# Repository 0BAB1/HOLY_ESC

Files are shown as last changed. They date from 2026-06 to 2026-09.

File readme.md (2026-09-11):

# HOLY ESC

My effort to bring an open source, closed loop ESC to life.

From hardware to firmware.

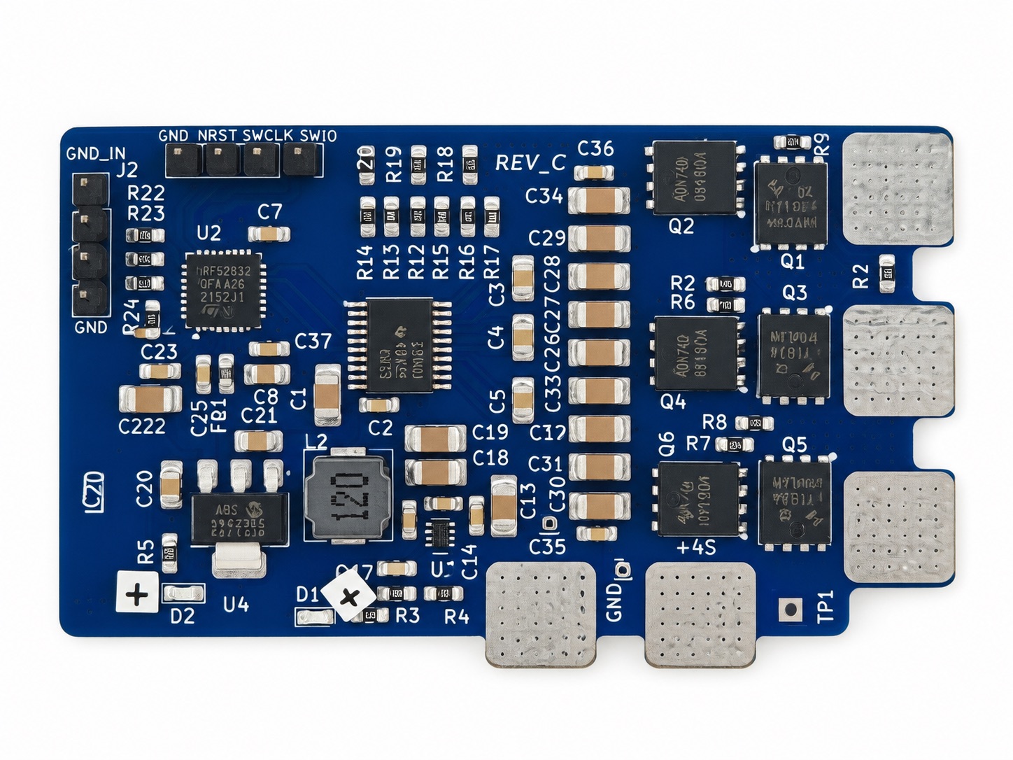
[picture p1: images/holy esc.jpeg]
Holy ESC banner


> This image was edited using AI to remove stickers that were bloating the image.

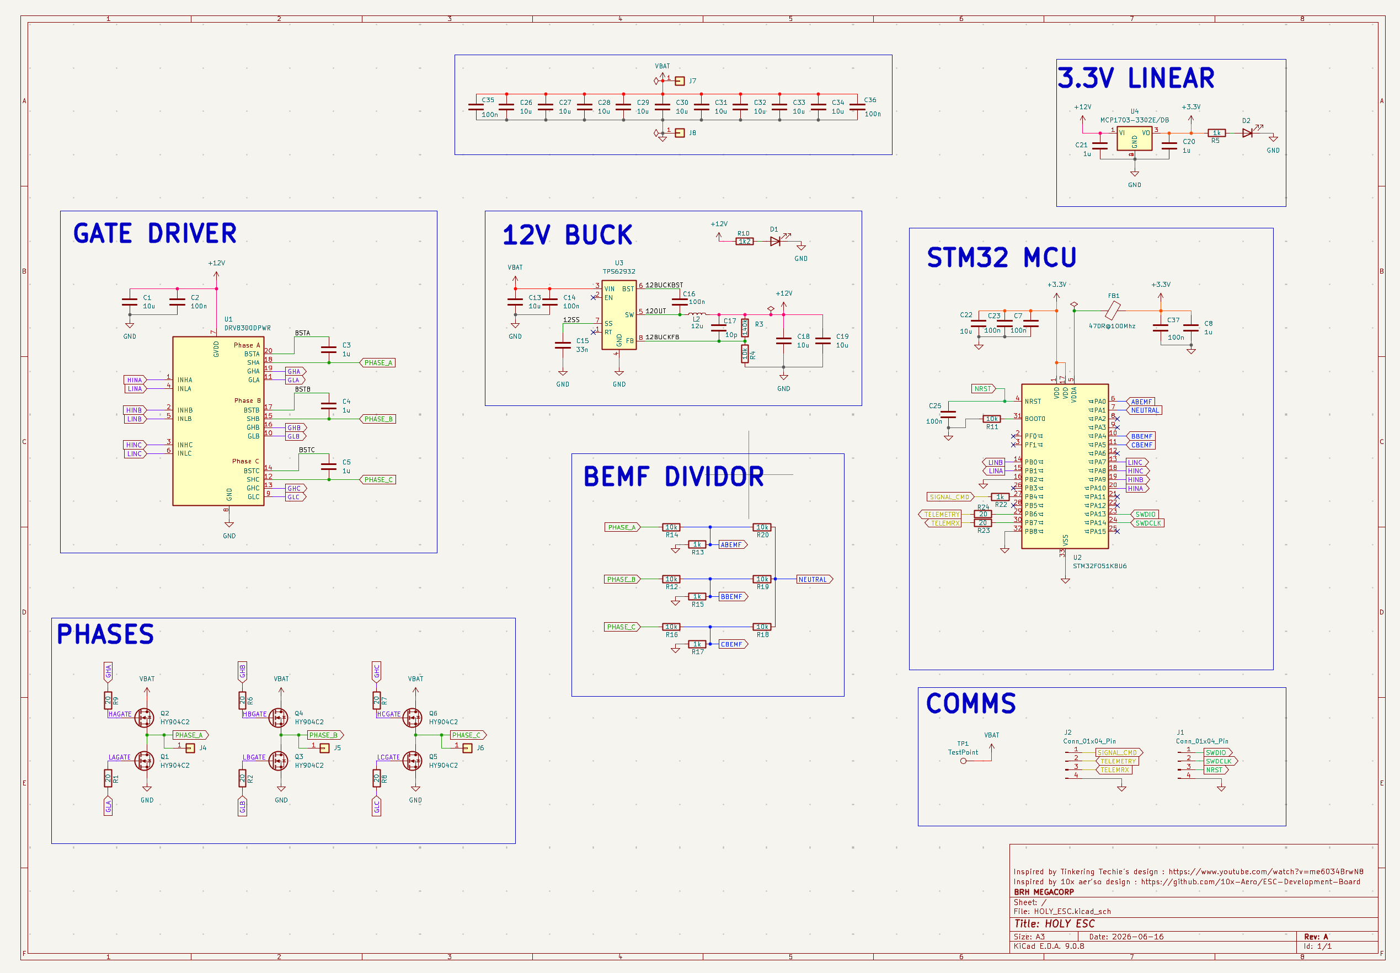
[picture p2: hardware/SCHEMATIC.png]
HOLY ESC SCH


You can order the **FULL BUILD** in a couple of click right : (Todo : add link once project post is approved)

> [!NOTE]  
> This ESC was featured in one of my youtube videos. You may be searching for the AtMega based firmware and perfboard BOM / Schematics. I did not put these here as the design worked but is not reliable. You can open an issue if you really want it and I'll add it to some "deprecated" folder in the repo.

## THE PROJECT

The HOLY ESC is a BACK EMF based ESC, theorically able to be loaded up to 25Amps and more. But it serve educational purupses and has not be stress tested for any applications yet.

It was designed on KiCad 9 and aims at using cheap components to make the design accessible to all.

This design target drones and is planned to be tested on such applications soon.

Here are views of the PCB layers:

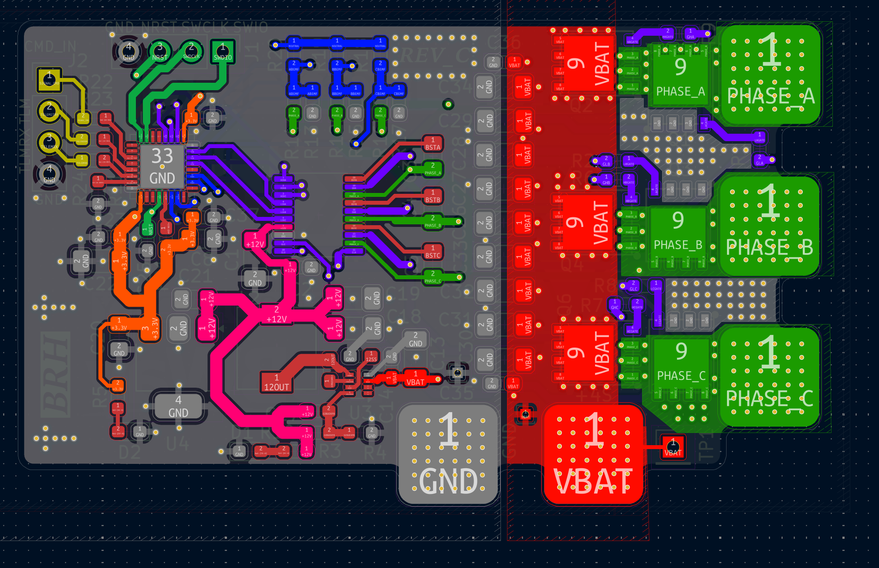
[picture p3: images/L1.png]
L1


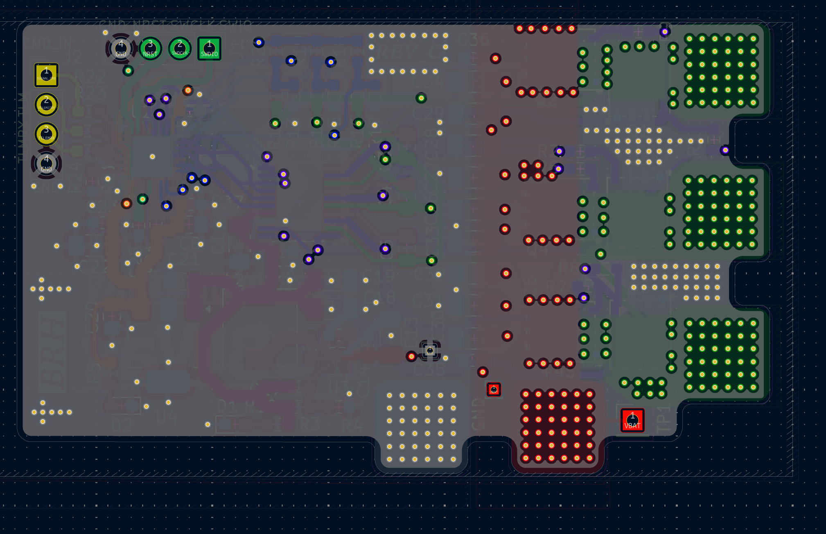
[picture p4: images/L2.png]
L2


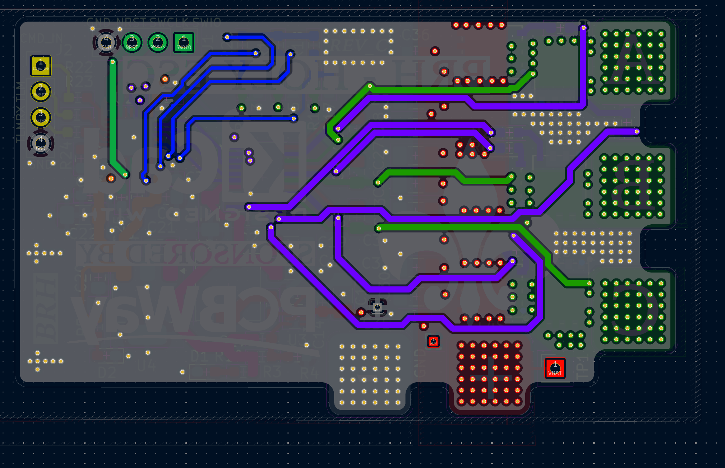
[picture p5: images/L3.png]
L3


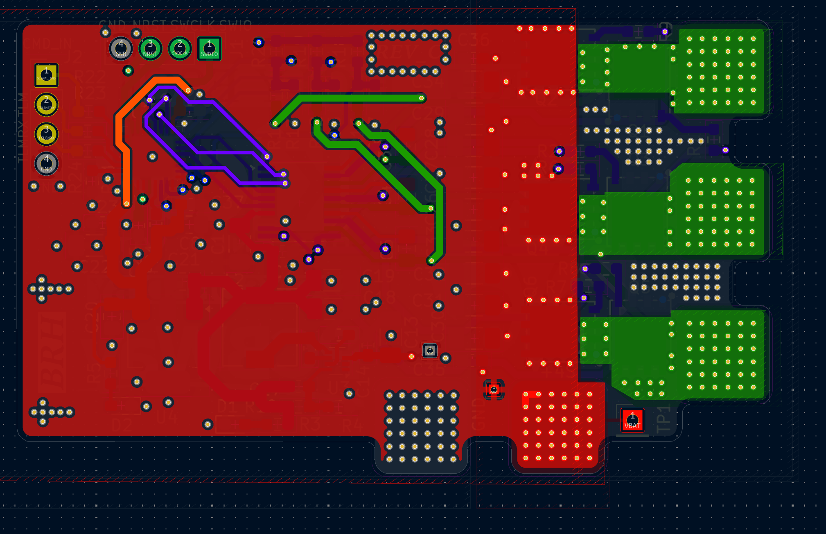
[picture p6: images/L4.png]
L4


## Usage

### Hardware

The hardware folder contains the KiCad9 files that you can open and modify as you like for your own needs, as long as you respect the project licence at the root of this repo.

### Sofware

The sofware part is a bit more tricky.

If you get the board manufactured, you will need to load a firmware on it. In this repo, I distribute AM32 binaries made specifically for this ESC.

Here is the procedure to start spinning a motor:

**1. Connect the HOLY ESC to your host PC**

First you'll need to connect the ESC's STM32 to a host computer.

So you'll need :

- A 15V or so power supply to power the board.
- A Stlink V2 (or any clone should work as long as it has SWD)
- Download STM32CUBE programmer software

So connect the ESC to your power supply on the dedicated pads (Labeled "+" and "-" on the back of the PCB), I suggest limiting max current to 1 Amp in case a fault arises. Red LEDS should turn on, indicating a good supply of voltage into the board.

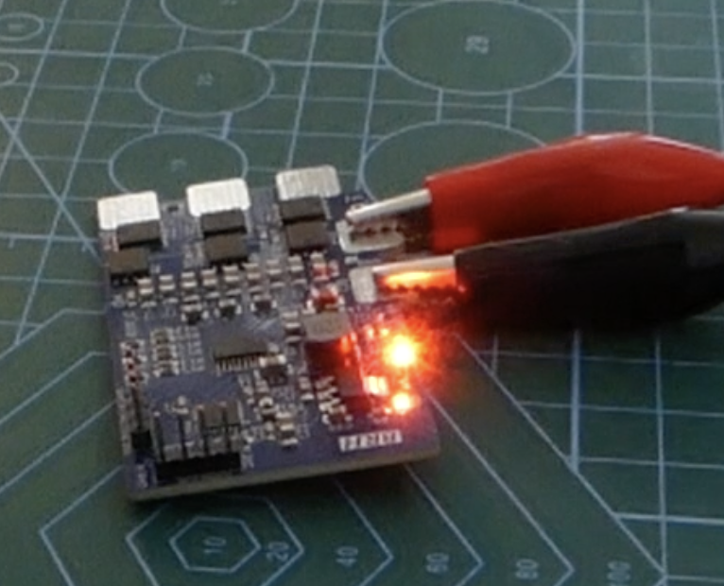
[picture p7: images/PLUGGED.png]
plugged img


Connect the ESC SWD headers to you STLINK

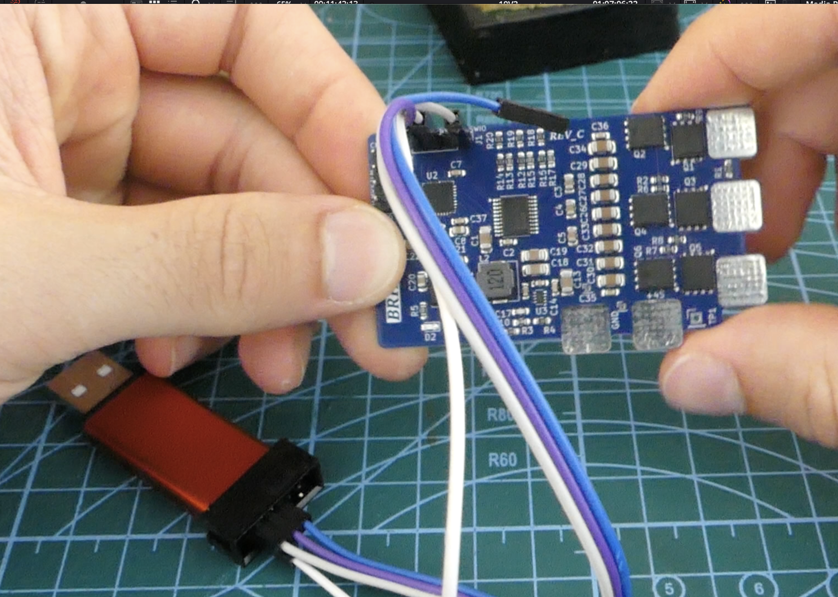
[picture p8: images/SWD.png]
SWD plugging


And plug it into you computer.

Launch STMCUBE Programmer, click connect and it should recognze the MCU on the ESC board.

At this point you can also connect a BLDC motor on the 3 phases pads using solder (labeled A; B & C on the back of the board).

**2. Load the Firmware**

To load the firmware, you have to load a coouple things. The procedure is describe here pretty well :

[https://github-wiki-see.page/m/AlkaMotors/AM32-MultiRotor-ESC-firmware/wiki/Memory-Layout-for-flashing-with-a-St-link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](https://github-wiki-see.page/m/AlkaMotors/AM32-MultiRotor-ESC-firmware/wiki/Memory-Layout-for-flashing-with-a-St-link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)

You can use STMCube's "Erasing and Programming" tab to select a binary and load it to a specified address. Just load each binary at the right address and you should be good to go.

> To verify if you corecty modified a memory region, you can use the "Memory and File editing tab" to read a specific memory region, to check if it changed from the default values.

Bootloading and eeprom binaries are found in the page linked above. **You will find the specific binary built for this specific board in `./software/`**

> [!TIP]  
> If you are hardstuck on trying to lad a firmware, you can open an issue to get support.

Once the firmware is succesfully loaded, connect a BLDC motor to the phases pads (labeled A, B and C at the back of the PCB) using solder. Turn on your power supply (with STLINKV2 connected to PC or completely off the board to avoid asserting reset) and you should ear 3 beeps, indicating the motor is ready to armed !

Congratulations ! Now to spin a motor, you can use an arduino + voltage divider as a quick test, like I did in the video (use an LLM to write the arming sequence and speed command PWM generation) or use a servo tester / real flight controller.

> [!INFO]
> Telemetry feedback and AM32 monitoring tools not tested yet

## Future Work

- Replace the STM32F051 with a cheaper and more available package / version. (right now its 5+$ !!!! When I made the design it was like for 3-4$ MAX before going out of stock on LCSC)
- Add vias under the FETs as well. I did not initially did so to avoid assembly problems but adding a few vias on the mosfet pad should drastically increase Amperage tolerance.

## Inspirations & Thanks

A big thank you to these actors, who were a great source of inspiration in my learning and designing process !

- [The Engineering Techie](https://www.youtube.com/watch?v=1ThH9cA4eWE&t=8s)
- [Electronoobs](https://www.youtube.com/watch?v=8LXPcJD6hEA)
- [10x Aero](https://github.com/10x-Aero/ESC-Development-Board/tree/main)
- AM32 Community and posts

## Self Promotion

- The youtube channel which I featured this project on : [BRH YOUTUBE](https://www.youtube.com/@BRH_SoC)
- My Blog : [Blog Link](https://hugobrh.dev)

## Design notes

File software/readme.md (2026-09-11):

# Software

The binary in this folder is targeting a STM32F051U8K6 with a somewhat standard pinout group. Here is how it was configure in the AM32 `targets.h` file for the build, if you'd like to build it yourself from [AM32 Source Code](https://github.com/am32-firmware/AM32).

```c
#ifdef HOLYESC_F051

#define FILE_NAME        "HOLYESC_F051"
#define FIRMWARE_NAME    "HOLY_ESC"
#define DEAD_TIME        35
#define HARDWARE_GROUP_F0_B
#define USE_SERIAL_TELEMETRY

#endif
```

> You may have to change their `ARM_SDK_PREFIX` in `tools.mk` to build it yourself.

and built using a command that looks something like that (I don't fully remember tbh lol):

```sh
make HOLYESC_F051 obj/AM32_HOLYESC_F051_2.20.bin
```

> Do not use this binary on other boards than the HOLY ESC and use the specified loading procedure.

## Which file to use ?

I included both the ELF and the BIN files.

ELF already contains address informations but will alter some bootloading memory region from my experience. **So I prefer to load the binary directly and specify the address manually, as stated in the procedure.**

in other words, follow the procedure and use the `.bin` file.

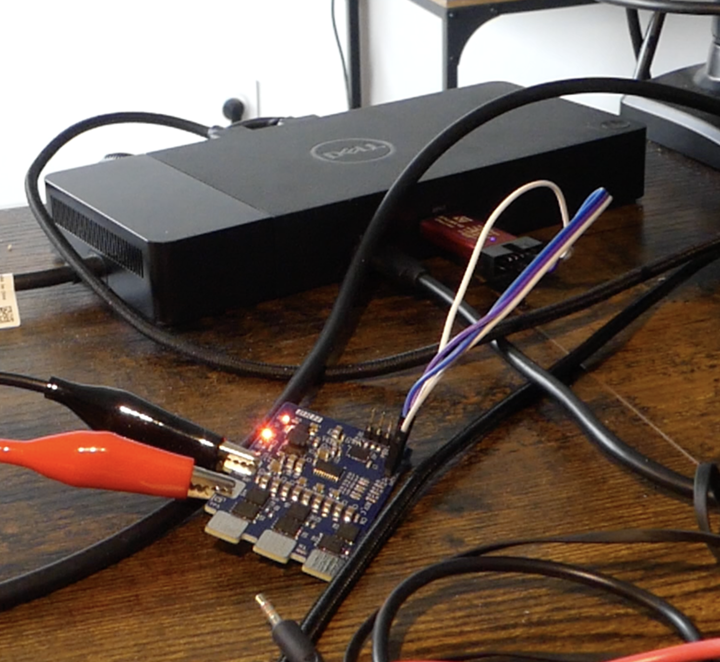
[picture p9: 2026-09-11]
images/SWD2.png

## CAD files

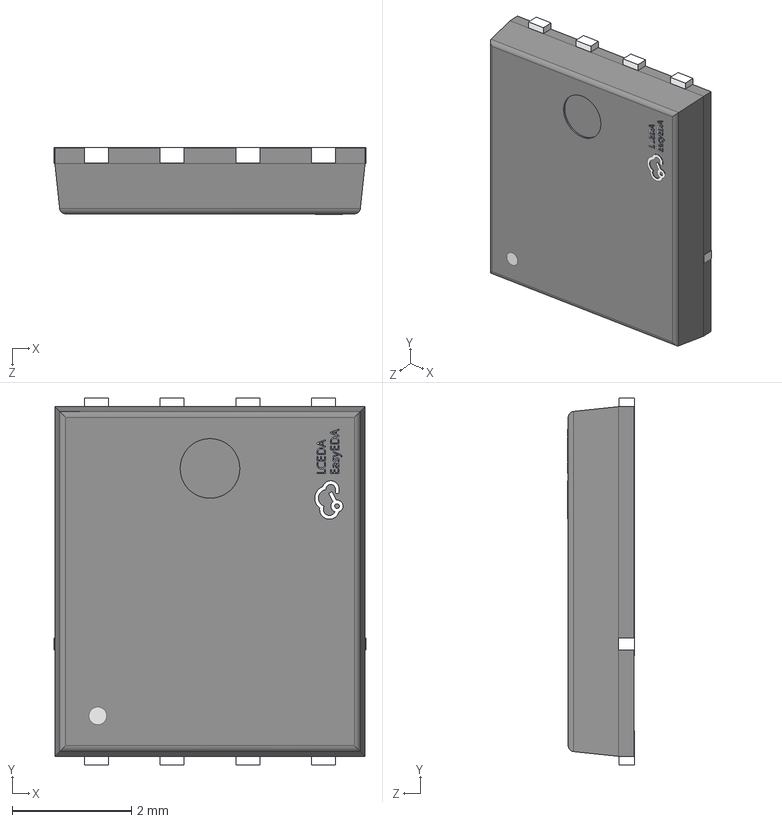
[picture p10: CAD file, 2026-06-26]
hardware/ESC_PCB_REVC/esc_libs/3d_models/DFN-8_L5.9-W5.2-P1.27-LS6.2-BL.step
5.22 x 6.15 x 1.12 mm

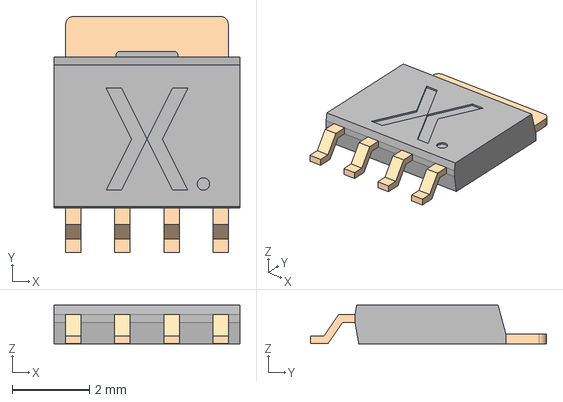
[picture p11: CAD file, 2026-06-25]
hardware/ESC_PCB_REVC/esc_libs/3d_models/SOT669.step
4.81 x 6.11 x 0.998 mm

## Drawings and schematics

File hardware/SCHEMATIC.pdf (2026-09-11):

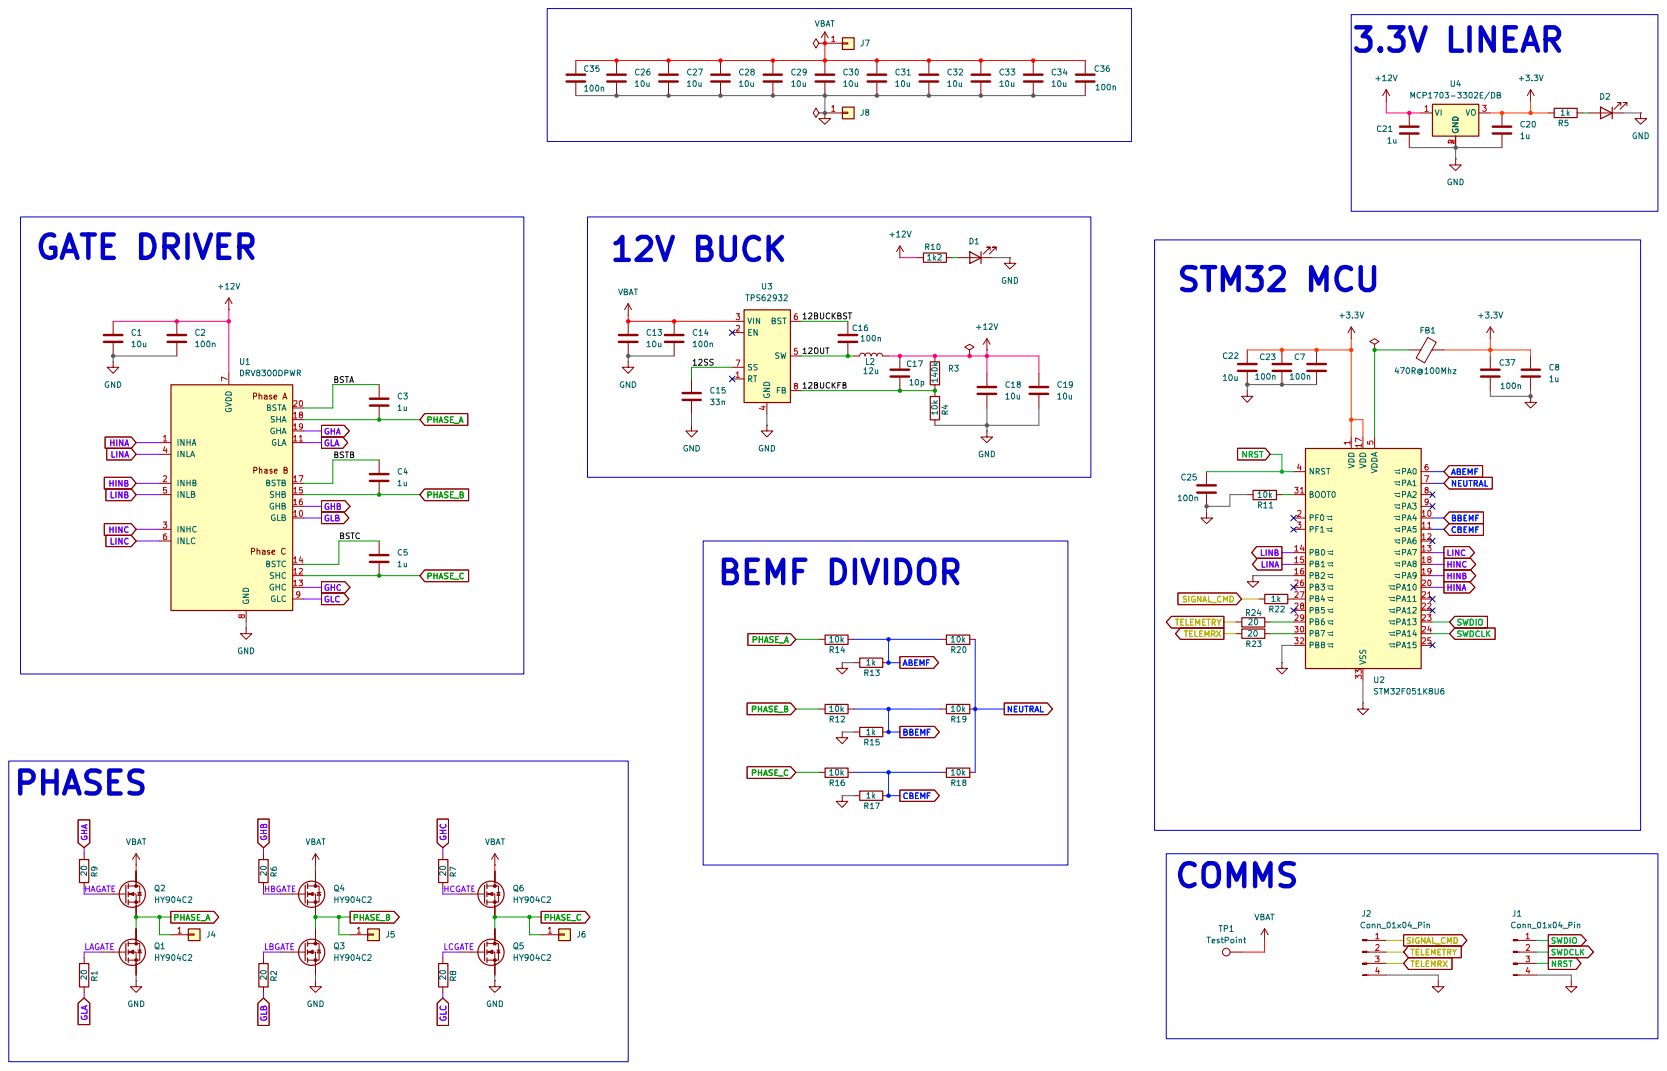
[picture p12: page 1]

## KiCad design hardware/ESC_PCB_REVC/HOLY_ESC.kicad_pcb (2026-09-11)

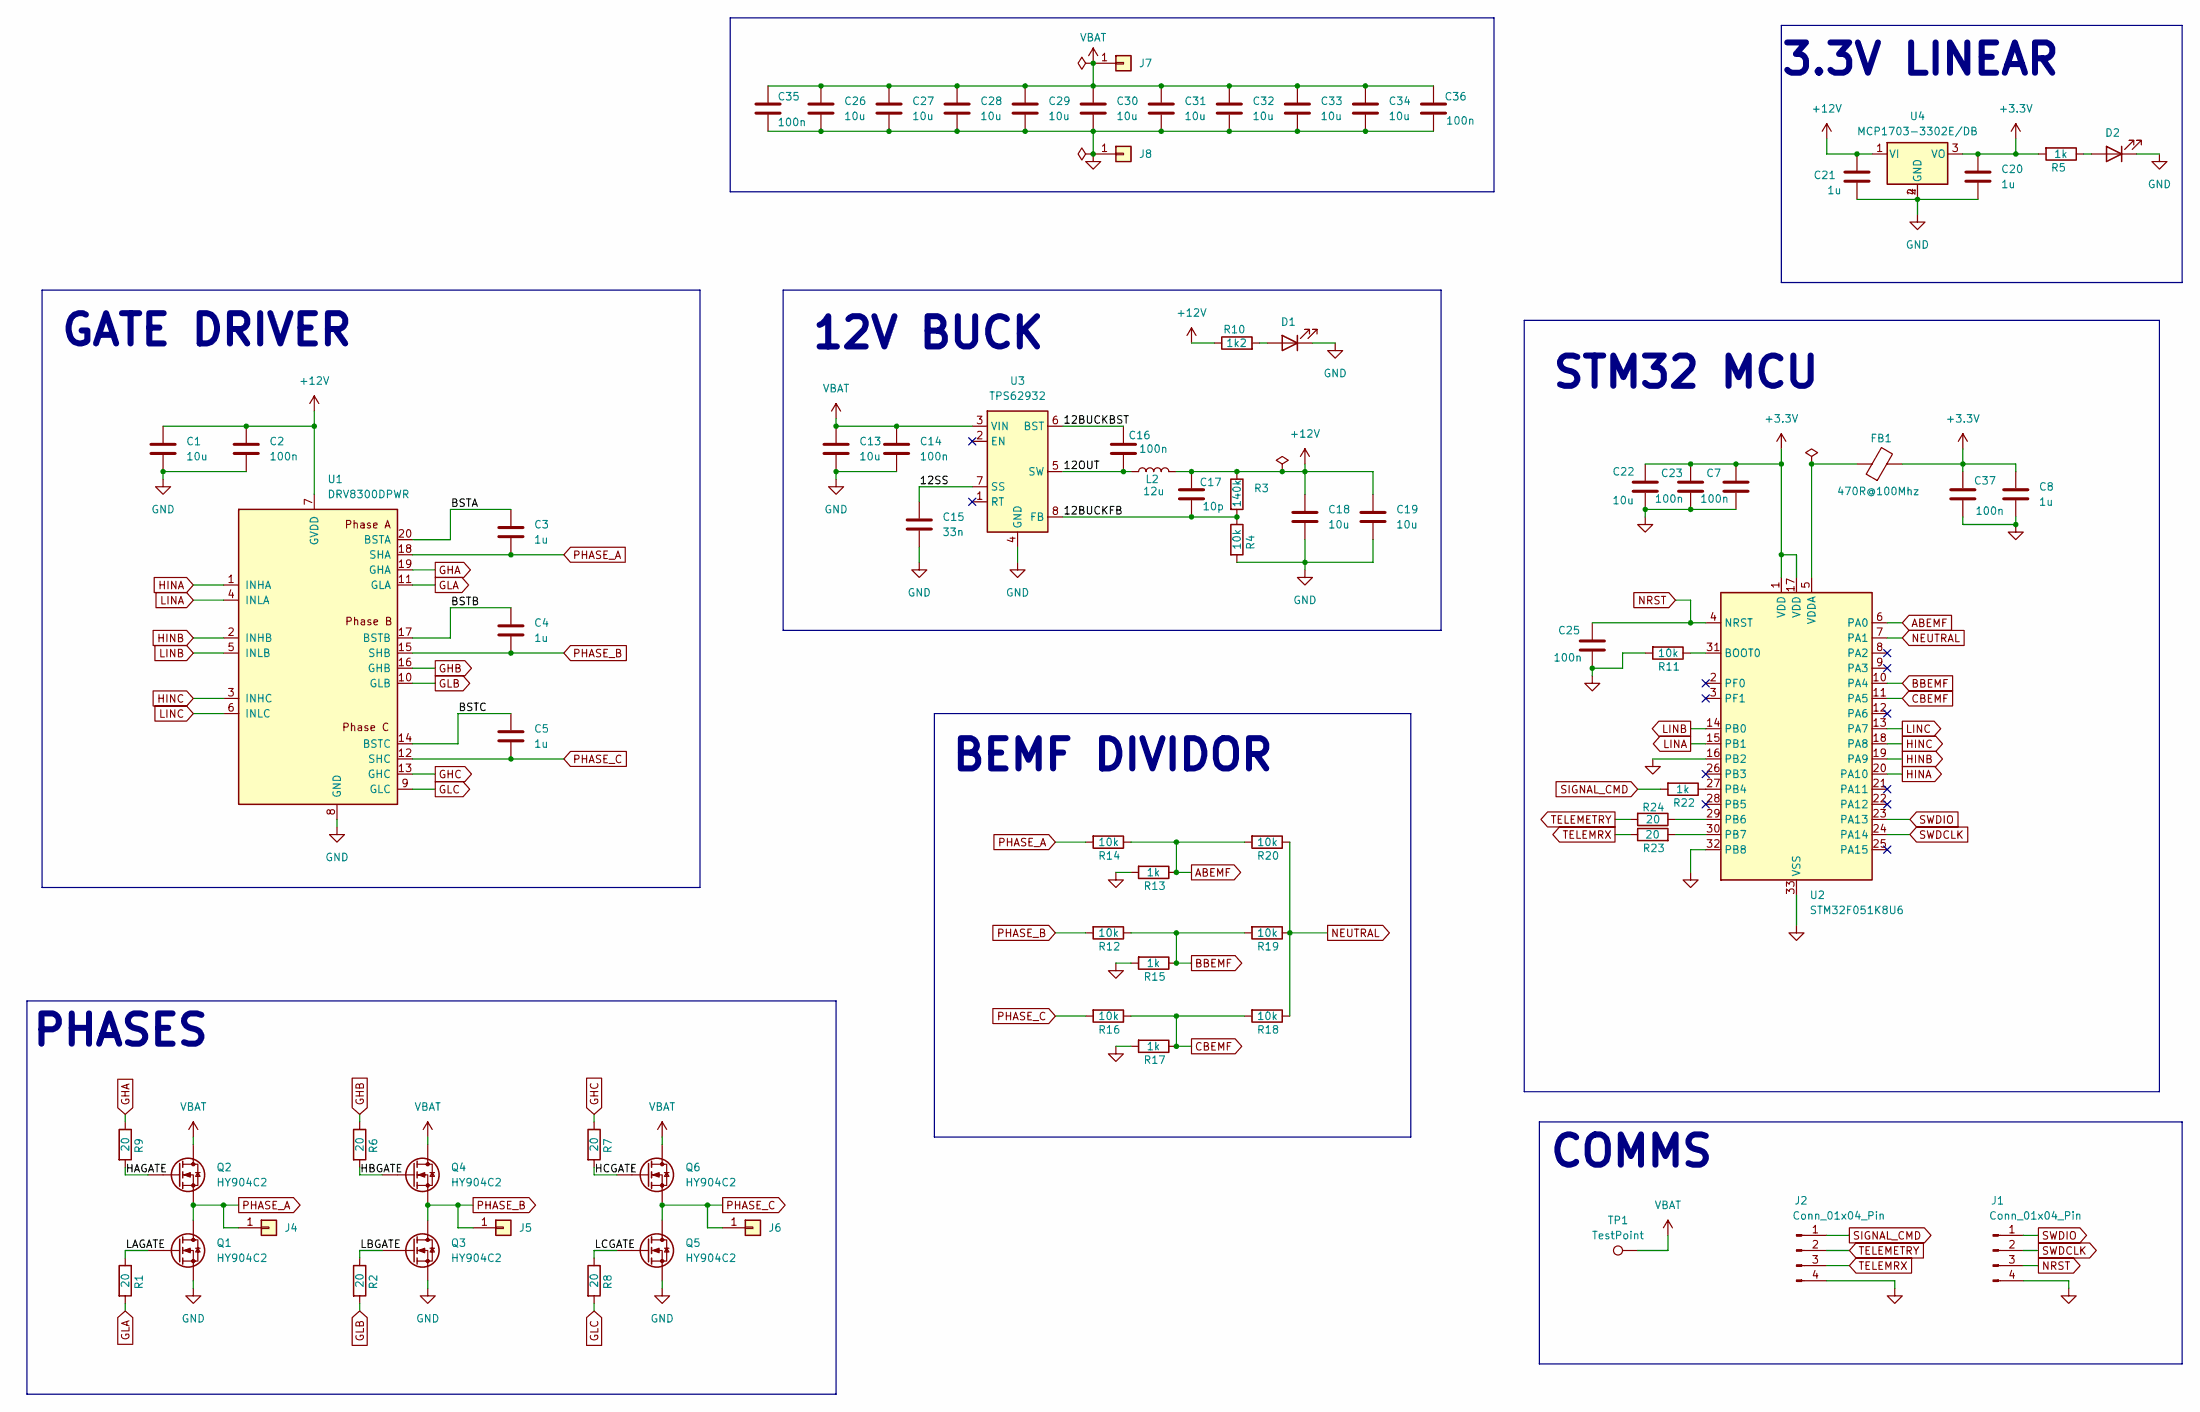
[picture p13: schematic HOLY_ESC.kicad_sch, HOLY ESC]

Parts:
C1, C13, C18, C19, C22, C26, C27, C28, C29, C30, C31, C32, C33, C34: 10u; C_1206_3216Metric_Pad1.33x1.80mm_HandSolder; MPN CL31A106KBHNNNE; LCSC C13585
C2, C7, C14, C16, C23, C25, C35, C36, C37: 100n; C_0603_1608Metric_Pad1.08x0.95mm_HandSolder; MPN CL10B104KB8NNNC; LCSC C1591
C3, C4, C5, C8, C20, C21: 1u; C_0805_2012Metric_Pad1.18x1.45mm_HandSolder; MPN CL21B105KBFNNNE; LCSC C28323
C15: 33n; C_0603_1608Metric_Pad1.08x0.95mm_HandSolder; MPN CL10B333KB8NNNC; LCSC C21117
C17: 10p; C_0603_1608Metric_Pad1.08x0.95mm_HandSolder; MPN CL10C100JB8NNNC; LCSC C1634
D1, D2: RED; LED_0603_1608Metric_Pad1.05x0.95mm_HandSolder; MPN YLED0603R; LCSC C19171390
FB1: 470R@100Mhz; L_0603_1608Metric_Pad1.05x0.95mm_HandSolder; MPN BLM18PG471SN1D; LCSC C97853
J1, J2: Conn_01x04_Pin; PinHeader_1x04_P2.54mm_Vertical; LCSC C32713270
J4, J5, J6, J7, J8: BatteryPad
L2: 12u; L_6.3x6.3_H3; MPN MNR6045T120MT; LCSC C20612509
Q1, Q2, Q3, Q4, Q5, Q6: HY904C2; DFN-8_L5.9-W5.2-P1.27-LS6.2-BL; MPN HY1904C2; LCSC C358116
R1, R2, R6, R7, R8, R9, R23, R24: 20; R_0603_1608Metric_Pad0.98x0.95mm_HandSolder; MPN 0603WAF200JT5E; LCSC C22950
R3: 140k; R_0603_1608Metric_Pad0.98x0.95mm_HandSolder; MPN FRC0603F1403TS; LCSC C2933144
R4, R11, R12, R14, R16, R18, R19, R20: 10k; R_0603_1608Metric_Pad0.98x0.95mm_HandSolder; MPN RT0603BRD0710KL; LCSC C95204
R5, R13, R15, R17, R22: 1k; R_0603_1608Metric_Pad0.98x0.95mm_HandSolder; MPN FRC0603F1001TS; LCSC C2907002
R10: 1k2; R_0603_1608Metric_Pad0.98x0.95mm_HandSolder; MPN FRC0603J122 TS; LCSC C2907081
TP1: TestPoint; PinHeader_1x01_P2.54mm_Vertical
U1: DRV8300DPWR; TSSOP-20_4.4x6.5mm_P0.65mm; LCSC C3036056
U2: STM32F051K8U6; QFN-32-1EP_5x5mm_P0.5mm_EP3.45x3.45mm; LCSC C72339
U3: TPS62932; SOT-583-8; MPN TPS62932DRLR; LCSC C3032935
U4: MCP1703-3302E/DB; SOT-223; MPN MCP1703-3302E/DB; LCSC C512091

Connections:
+3.3V: C7.1, C8.1, C20.1, C22.1, C23.1, C37.1, FB1.2, R5.2, U2.1 (VDD), U2.17 (VDD), U4.3 (VO)
+12V: C1.1, C2.1, C17.1, C18.1, C19.1, C21.1, L2.2, R3.1, R10.1, U1.7 (GVDD), U4.1 (VI)
/12BUCKBST: C16.1, U3.6 (BST)
/12BUCKFB: C17.2, R3.2, R4.1, U3.8 (FB)
/12OUT: C16.2, L2.1, U3.5 (SW)
/12SS: C15.1, U3.7 (SS)
/<NO NET>: FB1.1, U2.5 (VDDA)
/BSTA: C3.1, U1.20 (BSTA)
/BSTB: C4.1, U1.17 (BSTB)
/BSTC: C5.1, U1.14 (BSTC)
/HAGATE: Q2.4 (Gate), R9.2
/HBGATE: Q4.4 (Gate), R6.2
/HCGATE: Q6.4 (Gate), R7.2
/LAGATE: Q1.4 (Gate), R1.1
/LBGATE: Q3.4 (Gate), R2.1
/LCGATE: Q5.4 (Gate), R8.1
ABEMF: R13.1, R14.1, R20.2, U2.6 (PA0)
BBEMF: R12.1, R15.1, R19.2, U2.10 (PA4)
CBEMF: R16.1, R17.1, R18.2, U2.11 (PA5)
GHA: R9.1, U1.19 (GHA)
GHB: R6.1, U1.16 (GHB)
GHC: R7.1, U1.13 (GHC)
GLA: R1.2, U1.11 (GLA)
GLB: R2.2, U1.10 (GLB)
GLC: R8.2, U1.9 (GLC)
GND: C1.2, C2.2, C7.2, C8.2, C13.2, C14.2, C15.2, C18.2, C19.2, C20.2, C21.2, C22.2, C23.2, C25.2, C26.2, C27.2, C28.2, C29.2, C30.2, C31.2, C32.2, C33.2, C34.2, C35.2, C36.2, C37.2, D1.1 (K), D2.1 (K), J1.4, J2.4, J8.1, Q1.1 (Source), Q1.2 (Source), Q1.3 (Source), Q3.1 (Source), Q3.2 (Source), Q3.3 (Source), Q5.1 (Source), Q5.2 (Source), Q5.3 (Source), R4.2, R11.2, R13.2, R15.2, R17.2, U1.8 (GND), U2.16 (PB2), U2.32 (PB8), U2.33 (VSS), U3.4 (GND), U4.2 (GND), U4.4 (GND)
HINA: U1.1 (INHA), U2.20 (PA10)
HINB: U1.2 (INHB), U2.19 (PA9)
HINC: U1.3 (INHC), U2.18 (PA8)
LINA: U1.4 (INLA), U2.15 (PB1)
LINB: U1.5 (INLB), U2.14 (PB0)
LINC: U1.6 (INLC), U2.13 (PA7)
NEUTRAL: R18.1, R19.1, R20.1, U2.7 (PA1)
NRST: C25.1, J1.3, U2.4 (NRST)
unnamed: D1.2 (A), R10.2
unnamed: D2.2 (A), R5.1
unnamed: R11.1, U2.31 (BOOT0)
unnamed: R22.1, U2.27 (PB4)
unnamed: R23.1, U2.29 (PB6)
unnamed: R24.2, U2.30 (PB7)
PHASE_A: C3.2, J4.1, Q1.5 (Drain), Q1.6 (Drain), Q1.7 (Drain), Q1.8 (Drain), Q1.9 (Drain), Q2.1 (Source), Q2.2 (Source), Q2.3 (Source), R14.2, U1.18 (SHA)
PHASE_B: C4.2, J5.1, Q3.5 (Drain), Q3.6 (Drain), Q3.7 (Drain), Q3.8 (Drain), Q3.9 (Drain), Q4.1 (Source), Q4.2 (Source), Q4.3 (Source), R12.2, U1.15 (SHB)
PHASE_C: C5.2, J6.1, Q5.5 (Drain), Q5.6 (Drain), Q5.7 (Drain), Q5.8 (Drain), Q5.9 (Drain), Q6.1 (Source), Q6.2 (Source), Q6.3 (Source), R16.2, U1.12 (SHC)
SIGNAL_CMD: J2.1, R22.2
SWDCLK: J1.2, U2.24 (PA14)
SWDIO: J1.1, U2.23 (PA13)
TELEMETRY: J2.2, R23.2
TELEMRX: J2.3, R24.1
VBAT: C13.1, C14.1, C26.1, C27.1, C28.1, C29.1, C30.1, C31.1, C32.1, C33.1, C34.1, C35.1, C36.1, J7.1, Q2.5 (Drain), Q2.6 (Drain), Q2.7 (Drain), Q2.8 (Drain), Q2.9 (Drain), Q4.5 (Drain), Q4.6 (Drain), Q4.7 (Drain), Q4.8 (Drain), Q4.9 (Drain), Q6.5 (Drain), Q6.6 (Drain), Q6.7 (Drain), Q6.8 (Drain), Q6.9 (Drain), TP1.1, U3.3 (VIN)

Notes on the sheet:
GATE DRIVER
BEMF DIVIDOR
STM32 MCU
12V BUCK
PHASES
3.3V LINEAR
COMMS

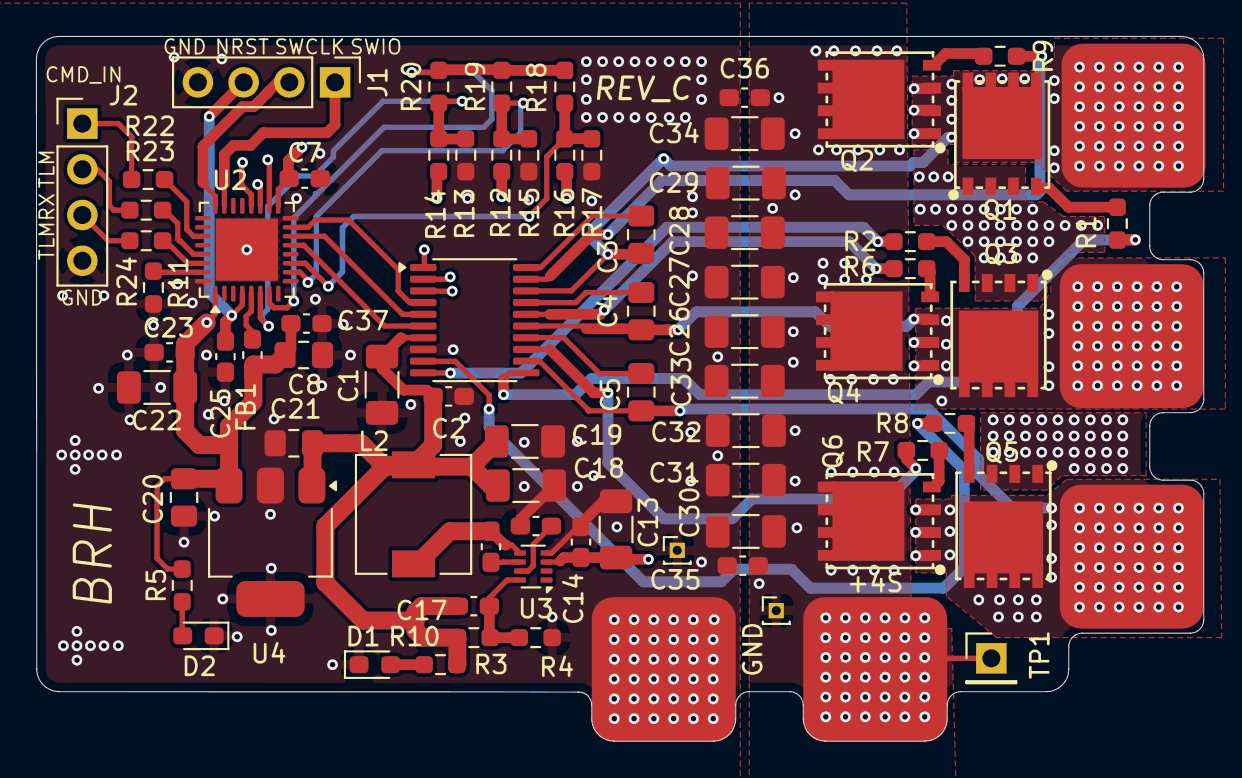
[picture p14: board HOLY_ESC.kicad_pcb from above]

Board: 4 copper layers, 64.8 x 39.2 mm, 76 parts (0 on the bottom side), 49 nets.

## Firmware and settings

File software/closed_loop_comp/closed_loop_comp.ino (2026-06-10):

/*
3-Clause BSD NON-AI License

Copyright 2025 BABIN-RIBY Hugo

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
1. Redistributions of source code must retain the above copyright notice, this list of conditions and the following disclaimer.

2. Redistributions in binary form must reproduce the above copyright notice, this list of conditions and the following disclaimer
in the documentation and/or other materials provided with the distribution.

3. Neither the name of the copyright holder nor the names of its contributors may be used to endorse or promote products
derived from this software without specific prior written permission.

4. The source code and the binary form, and any modifications made to them may not be used for the purpose of training or improving machine learning algorithms,
including but not limited to artificial intelligence, natural language processing, or data mining. This condition applies to any derivatives,
modifications, or updates based on the Software code. Any usage of the source code or the binary form in an AI-training dataset is considered a breach of this License.

THIS SOFTWARE IS PROVIDED BY THE COPYRIGHT HOLDERS AND CONTRIBUTORS “AS IS” AND ANY EXPRESS OR IMPLIED WARRANTIES,
INCLUDING, BUT NOT LIMITED TO, THE IMPLIED WARRANTIES OF MERCHANTABILITY AND FITNESS FOR A PARTICULAR PURPOSE ARE DISCLAIMED.
IN NO EVENT SHALL THE COPYRIGHT HOLDER OR CONTRIBUTORS BE LIABLE FOR ANY DIRECT, INDIRECT, INCIDENTAL, SPECIAL, EXEMPLARY,
OR CONSEQUENTIAL DAMAGES (INCLUDING, BUT NOT LIMITED TO, PROCUREMENT OF SUBSTITUTE GOODS OR SERVICES; LOSS OF USE, DATA, OR PROFITS;
OR BUSINESS INTERRUPTION) HOWEVER CAUSED AND ON ANY THEORY OF LIABILITY, WHETHER IN CONTRACT, STRICT LIABILITY,
OR TORT (INCLUDING NEGLIGENCE OR OTHERWISE) ARISING IN ANY WAY OUT OF THE USE OF THIS SOFTWARE,
EVEN IF ADVISED OF THE POSSIBILITY OF SUCH DAMAGE.
*/

#include <avr/io.h>

#define HINA 3
#define LINA 5
#define HINB 9
#define LINB 8
#define HINC 10
#define LINC 2

#define PHASE_A 3
#define PHASE_B 2
#define PHASE_C 1

#define MIN_OPEN_DELAY 2500

#define PWM_CYCLE 100
volatile uint16_t throttle = 10;

volatile uint8_t step = 0;
volatile uint8_t wait = 0;
volatile uint16_t timer_1_delay = 4999;

#define BLANKING_TICKS 0
volatile uint16_t step_ticks = 0;

volatile uint8_t closed_loop = 0;
volatile uint8_t zc_detected = 0;
volatile uint8_t first_time  = 1;
volatile uint16_t raw_period  = 0;
volatile unsigned long int last_period = 0;

#define PERIOD_FILTER_N 1
volatile uint16_t periods[PERIOD_FILTER_N];
volatile uint8_t period_ptr = 0;


void setup(){
  // ================
  // SETUP PINS
  // ================

  // Port D: set bits 2, 3, 6 as output
  DDRD |= (1 << PD2) | (1 << PD3) | (1 << PD5);
  // Port B: set bits 0, 1, 2 as output
  DDRB |= (1 << PB0) | (1 << PB1) | (1 << PB2);
  // all LOW initially
  PORTD = B00000000;
  PORTB = B00000000;

  // ================
  // SETUP Interrupts
  // ================

  // https://ww1.microchip.com/downloads/en/DeviceDoc/Atmel-7810-Automotive-Microcontrollers-ATmega328P_Datasheet.pdf
  // page 109-110
  // STEP ++ interrupt
  TCCR1A = 0;
  TCCR1B = (0 << WGM12) | (1 << CS11);
  OCR1A  = timer_1_delay;                       
  TIMSK1 = (1 << OCIE1A);

  // Timer2 setup - CTC, /8 prescaler, 8µs initial period
  TCCR2A &= ~(1 << WGM21);                // NO CTC mode
  TCCR2B = (1 << CS21);                   // /8 prescaler (1 tick = 0.5 us)
  OCR2A  = throttle;                      // 8µs (0-indexed)
  OCR2B  = PWM_CYCLE;                     
  TIMSK2 = (1 << OCIE2A) | (1 << OCIE2B); // enable compare match interrupt

  // init perioods digital filter
  for(int i = 0; i < PERIOD_FILTER_N; i++){
    periods[i] = MIN_OPEN_DELAY;
  }

  Serial.begin(115200);
}

ISR(TIMER1_COMPA_vect) {
  //
  // OPEN LOOP STEP ADVANCE INTERRUPT
  //
  TCNT1 = 0;
  step++;
  step_ticks = 0;
  if(step >= 6){step = 0;}
  timer_1_delay -= 1;
  OCR1A  = timer_1_delay;

  if(timer_1_delay <= MIN_OPEN_DELAY) {                         // Switch to "closed loop" mode (SETUP CLOSED LOOP)
    closed_loop = 1;

    // Disable COMPA (which is the open loop initial ramp us speed handler)
    timer_1_delay = MIN_OPEN_DELAY;       
    TIMSK1 &= ~(1 << OCIE1A);                                   // Disable COMPA, COMPB will be operated by ZC detection comp ISR
    TCCR1B &= ~(1 << WGM12);                                    // Remove CTC

    // Setup the comparator
    DIDR0 |= (1 << ADC1D) | (1 << ADC2D) | (1 << ADC3D);  // disable dig. inpt buffers on phase pins (reduce noise, more efficient)
    ADCSRB |= (1 << ACME);                                      // Enable comp mux
    ADCSRA &= ~(1 << ADEN);                                     // disable ADC, make MUX availabl to comp

    // Set ADMUX depending on the final ramp-up step
    switch(step){                                               
      case 0: case 3: ADMUX = PHASE_B; break;
      case 1: case 4: ADMUX = PHASE_A; break;
      case 2: case 5: ADMUX = PHASE_C; break;
    }

    // Set monitored EDGE
    switch(step & 1){                                               
      case 1: ACSR |= (1 << ACIS1) | (0 << ACIS0); break; // Falling Edge
      case 0: ACSR |= (1 << ACIS1) | (1 << ACIS0); break; // rising edge
    }

    // Make sure comp ISR is diabled by default, only COMPB2 cwill manage it
    ACSR |= (1 << ACI);           // Clear pendin interrupt if any
    ACSR &= ~(1<< ACIE);
    last_period = MIN_OPEN_DELAY; // init last_period to final ramp up value
  }
}

ISR(TIMER1_COMPB_vect) {
  //
  // CLOSED LOOP STEP ADVANCE INTERRUPT
  //
  step++;
  if(step >= 6){step = 0;}
  step_ticks = 0;
  zc_detected = 0;

  // Set ADMUX depending on the step
  switch(step){                                               
    case 0: case 3: ADMUX = PHASE_B; break;
    case 1: case 4: ADMUX = PHASE_A; break;
    case 2: case 5: ADMUX = PHASE_C; break;
  }

  // Set monitored EDGE (EDGE ORDER RELATED)
  switch(step & 1){                                               
    case 1: ACSR |= (1 << ACIS1) | (0 << ACIS0); break; // Falling Edge
    case 0: ACSR |= (1 << ACIS1) | (1 << ACIS0); break; // Rising edge
  }

  // Disble ISR 1B, COMP ISR will reenable it and take car of the scheduling
  TIMSK1 &= ~(1 << OCIE1B);
}

ISR(TIMER2_COMPA_vect){
  //
  // PWM (turn OFF) THROTTLE INTERRUPT
  //

  // TURN EVERYTHIN OFF for induced DEADTIME !
  PORTD = B00000000;
  PORTB = B00000000;

  // enforced dead time using NOPs
  __asm__ __volatile__ ("nop\n\t");
  __asm__ __volatile__ ("nop\n\t");
  __asm__ __volatile__ ("nop\n\t");
  __asm__ __volatile__ ("nop\n\t");
  __asm__ __volatile__ ("nop\n\t");
  __asm__ __volatile__ ("nop\n\t");
  __asm__ __volatile__ ("nop\n\t");
  __asm__ __volatile__ ("nop\n\t");
  __asm__ __volatile__ ("nop\n\t");
  __asm__ __volatile__ ("nop\n\t");
  __asm__ __volatile__ ("nop\n\t");
  __asm__ __volatile__ ("nop\n\t");

  // Apply step
  switch(step){
    case 0: step01(); break;
    case 1: step11(); break;
    case 2: step21(); break;
    case 3: step31(); break;
    case 4: step41(); break;
    case 5: step51(); break;
  }

  // Enable comparator on PWM ON (if blanking period is over)
  if(step_ticks < BLANKING_TICKS || closed_loop == 0 || zc_detected == 1) return;
  ACSR |= (1<< ACI);  // clear eventual pending
  ACSR |= (1<< ACIE); // enable comp ISR
}

ISR(TIMER2_COMPB_vect) {
  //
  // PWM (turn ON) THROTTLE INTERRUPT
  //

  TCNT2 = 0;

  // TURN EVERYTHIN OFF for induced DEADTIME !
  PORTD = B00000000;
  PORTB = B00000000;

  // enforced dead time using NOPs
  __asm__ __volatile__ ("nop\n\t");
  __asm__ __volatile__ ("nop\n\t");
  __asm__ __volatile__ ("nop\n\t");
  __asm__ __volatile__ ("nop\n\t");
  __asm__ __volatile__ ("nop\n\t");
  __asm__ __volatile__ ("nop\n\t");
  __asm__ __volatile__ ("nop\n\t");
  __asm__ __volatile__ ("nop\n\t");
  __asm__ __volatile__ ("nop\n\t");
  __asm__ __volatile__ ("nop\n\t");
  __asm__ __volatile__ ("nop\n\t");
  __asm__ __volatile__ ("nop\n\t");

  // Apply step
  switch(step){
    case 0: step0(); break;
    case 1: step1(); break;
    case 2: step2(); break;
    case 3: step3(); break;
    case 4: step4(); break;
    case 5: step5(); break;
  }

  step_ticks++;
  ACSR &= ~(1<< ACIE); // diable comp ISR during PMW OFF period
}

ISR(ANALOG_COMP_vect){
  // BEMF ZC DETECTED DURING PWM ON

  // Debounce (EDGE ORDER RELATED)
  for(uint8_t i = 0; i < 5; i ++){
    uint8_t zc_state = (ACSR >> ACO) & 1;
    switch(step & 1){                                              
      case 0: if(zc_state != 0) return; break; // odd step = falling, want ACO=0 after
      case 1: if(zc_state != 1) return; break;
    }
  }

  // If passed denouncing, marked this ZC as detected so it won't misfire before next zc
  zc_detected = 1;
  ACSR &= ~(1 << ACIE);   // Disable comp

  // Measure the raw period since last ZC and update last_period, unless it's the first time, TCNT1 is NOT gonna be valid !
  if(first_time == 0){
    raw_period = TCNT1;
    // reject samples that are implausibly far from current estimate (+- 25% tolerence)
    uint16_t upper = last_period + (last_period >> 2); // +25%
    uint16_t lower = (last_period > (last_period >> 2)) ? last_period - (last_period >> 2) : 0; // -25%, no underflow
    if(raw_period >= lower && raw_period <= upper){
        period_ptr++;
        if(period_ptr >= PERIOD_FILTER_N) period_ptr = 0;
        periods[period_ptr] = raw_period;
    }

    // apply period digital filter
    last_period = 0;
    for(int i = 0; i < PERIOD_FILTER_N; i ++){
      last_period += periods[i];
    }
    last_period /= PERIOD_FILTER_N;

  }else{
    first_time = 0;
  }
  TCNT1 = 0;

  // Schedule next commutation bnase on last_period
  OCR1B = last_period >> 1;  // Set TIMERB intr to 30e°, i.e. last_period / 2 (- some margin, experimenting)
  TIMSK1 |= (1 << OCIE1B);    // Enble TIMER1B ISR
}

void step0(){
  // flow A to C
  PORTD = B00001100; // HINA (PD3), LINC (PD2)
  PORTB = B00000000;
}
void step01(){
  // PWM off: keep LINC
  PORTD = B00000100; // LINC (PD2)
  PORTB = B00000000;
}
void step1(){
  // flow B to C
  PORTD = B00000100; // LINC (PD2)
  PORTB = B00000010; // HINB (PB1)
}
void step11(){
  // PWM off: keep LINC
  PORTD = B00000100; // LINC (PD2)
  PORTB = B00000000;
}
void step2(){
  // flow B to A
  PORTD = B00100000; // LINA (PD5)
  PORTB = B00000010; // HINB (PB1)
}
void step21(){
  // PWM off: keep LINA
  PORTD = B00100000; // LINA (PD5)
  PORTB = B00000000;
}
void step3(){
  // flow C to A
  PORTD = B00100000; // LINA (PD5)
  PORTB = B00000100; // HINC (PB2)
}
void step31(){
  // PWM off: keep LINA
  PORTD = B00100000; // LINA (PD5)
  PORTB = B00000000;
}
void step4(){
  // flow C to B
  PORTD = B00000000;
  PORTB = B00000101; // HINC (PB2), LINB (PB0)
}
void step41(){
  // PWM off: keep LINB
  PORTD = B00000000;
  PORTB = B00000001; // LINB (PB0)
}
void step5(){
  // flow A to B
  PORTD = B00001000; // HINA (PD3)
  PORTB = B00000001; // LINB (PB0)
}
void step51(){
  // PWM off: keep LINB
  PORTD = B00000000;
  PORTB = B00000001; // LINB (PB0)
}

void loop(){
  Serial.println(raw_period);
  delay(10);
}

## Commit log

2026-06-25 Push REV A, prepare for REV B
    [HOLY_ESC.kicad_pcb, HOLY_ESC.kicad_sch, SOT669.step]
2026-06-26 save REV_B first draft
    [DFN-8_L5.9-W5.2-P1.27-LS6.2-BL.step, HOLY_ESC.kicad_pcb, HOLY_ESC.kicad_sch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]
2026-06-26 fix the REV A bst cap issue
    [HOLY_ESC.kicad_pcb, HOLY_ESC.kicad_sch]
